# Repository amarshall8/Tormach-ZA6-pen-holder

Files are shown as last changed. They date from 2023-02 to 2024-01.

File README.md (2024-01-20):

# Tormach-ZA6-pen-holder
 A compact, low cost, high precision pen drawing module for Tormach ZA6 robotic arms.\
 More info on the design can be found here https://www.alecmarshall.com/articles/tormach-za6-pen-plotter-module/
 
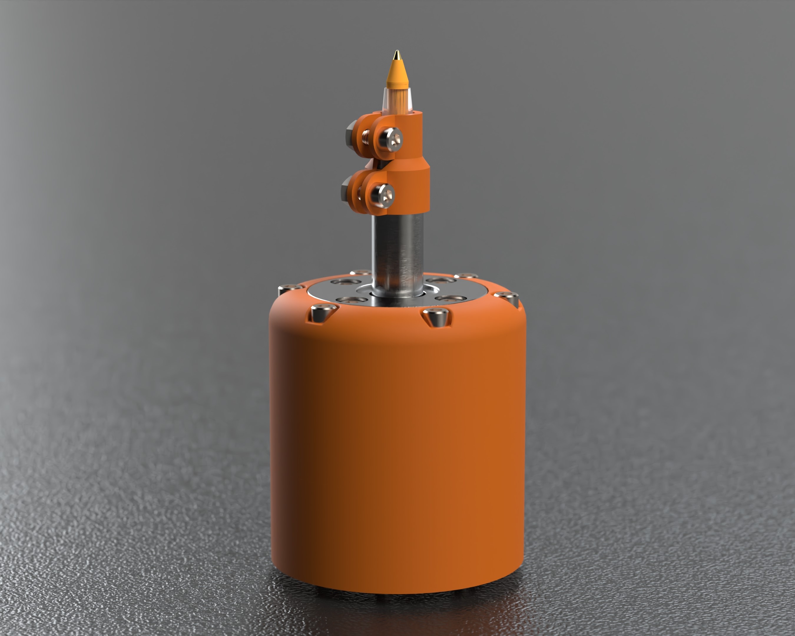
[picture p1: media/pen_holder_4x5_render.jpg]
render


## Required materials:

  * [Compression spring](https://www.mcmaster.com/9657K332/)
  * [12mm steel pipe](https://www.mcmaster.com/6045N11/)
  * [12mm linear bearing with circular flange](https://www.mcmaster.com/6483K114/) (Cheap LM12UU bearing with the same circular flange on eBay are what I used)
  * [1/8" by 1" Steel pin](https://www.mcmaster.com/90145A475/) (for endstop cross bar)
  * __10x__ 6-32 1/4" heat set inserts:
    * [Amazon](https://www.amazon.com/dp/B076R7F3DJ) (select long option)
    * [McMaster](https://www.mcmaster.com/93365A132/)
  * __6x__ 6-32 1-3/4" bolts/screws (To attach the upper section to the lower section)
  * __6x__ M4 25mm bolts/screws (Ideally SHCS. Attaches the lower section to the robotic arm)
  * __4x__ 6-32 1/2" bolts/screws (To attach the linear bearing to the upper section)
  * __2x__ 6-32 3/8" bolts/screws (For compression pen mount)
  * __2x__ 6-32 nuts (For compression pen mount)

## Assembly:

First the 3D printed parts need to have the heatset inserts pushed into the relevant spots on the parts. This should be fairly straightforward.\
There is an [excellent guide](https://hackaday.com/2019/02/28/threading-3d-printed-parts-how-to-use-heat-set-inserts/) for it on Hackaday with recommendations for slicer settings as well.

Next, you may need to sand down a section of the pipe to fit properly. The pipe is not always less than 12mm, and can trend upwards of it, meaning that it will not fit into the linear bearing. To solve this, you can mount the pipe in a drill, and have a second person use 400-600 grit sandpaper to slowly make it thin enough to slide smoothly. Make sure you wipe it with an oiled cloth before running it through the bearing, otherwise this will put metal dust into the bearing, which is not good.
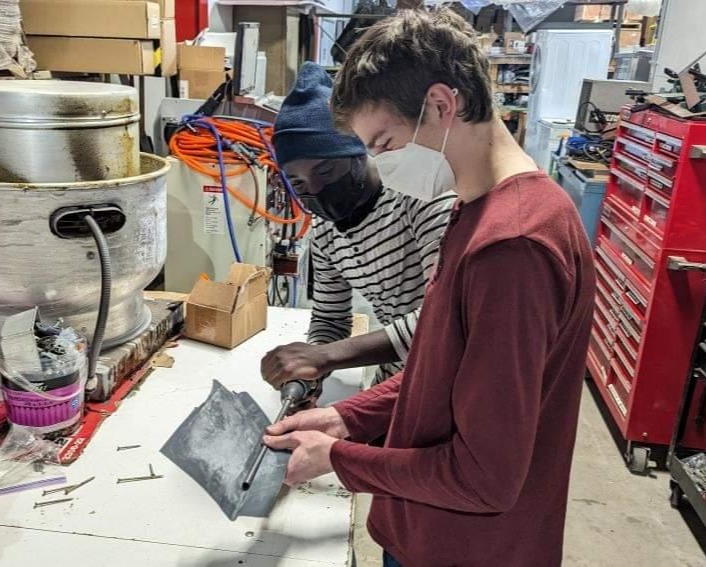
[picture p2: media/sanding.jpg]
sanding


Then, the section of pipe which has the correct diameter will need to be cut to the length specified in the drawing below. I recommend using a bandsaw or hacksaw for this.\
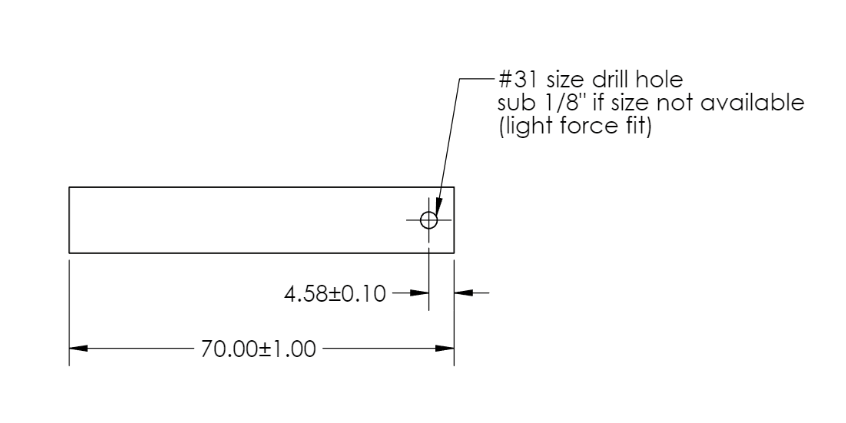
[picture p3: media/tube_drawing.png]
tube


To finish the pipe, a hole needs to be drilled at the distance from the edge specified in the drawing above to fit the 1/8 pin. This can be done by hand, but it is far easier with a drill press or a mill, since the pin can't be skewed much, otherwise it won't fit.
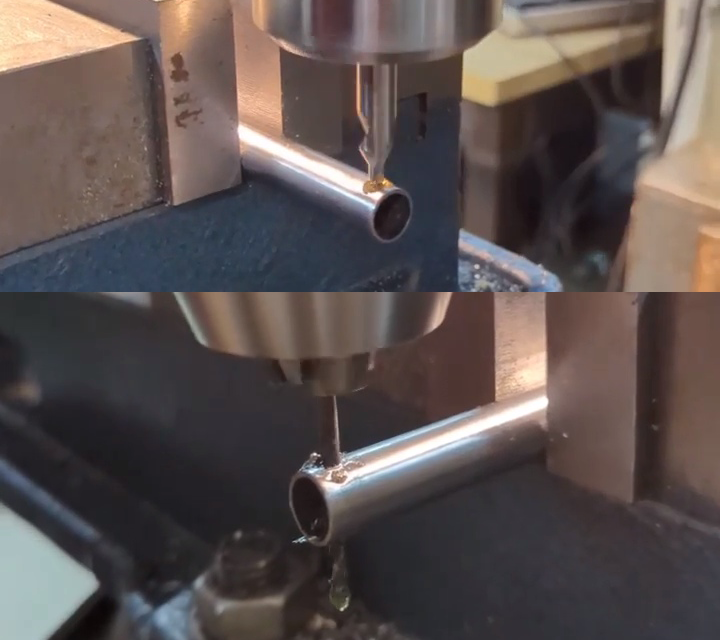
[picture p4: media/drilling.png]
drilling


Finally, the pin can be inserted into the pipe.
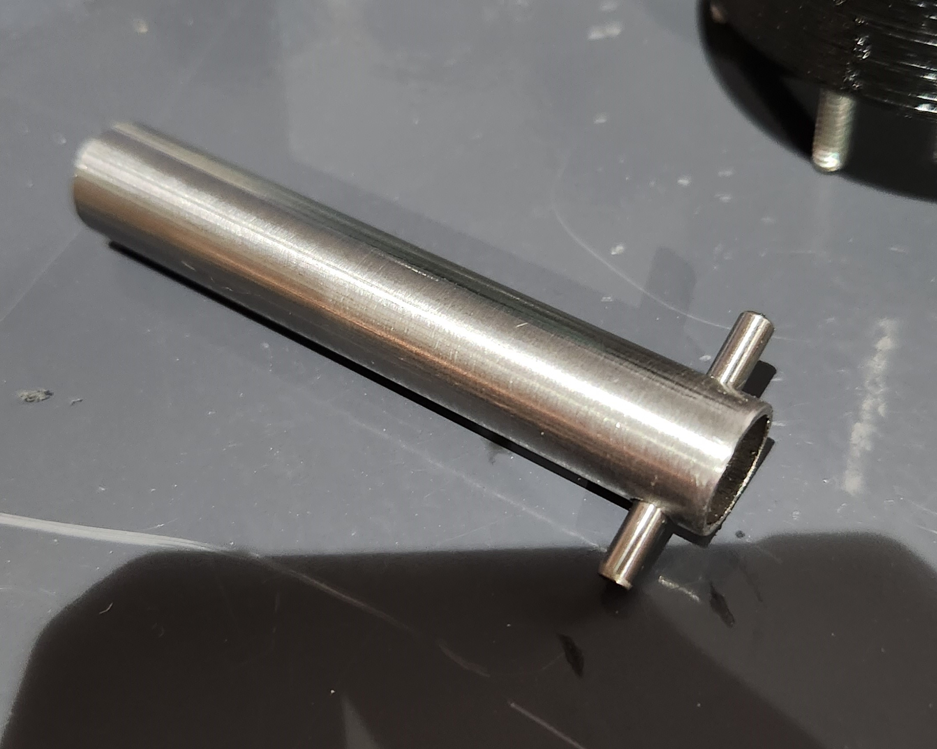
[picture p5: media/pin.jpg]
pin


The last step before assembling it onto the robot is to add the linear bearing to the upper housing 3D print and add the pipe. It should be semi press fit, just push it into the housing and add the four 6-32 1/2in screws to finish the upper housing.
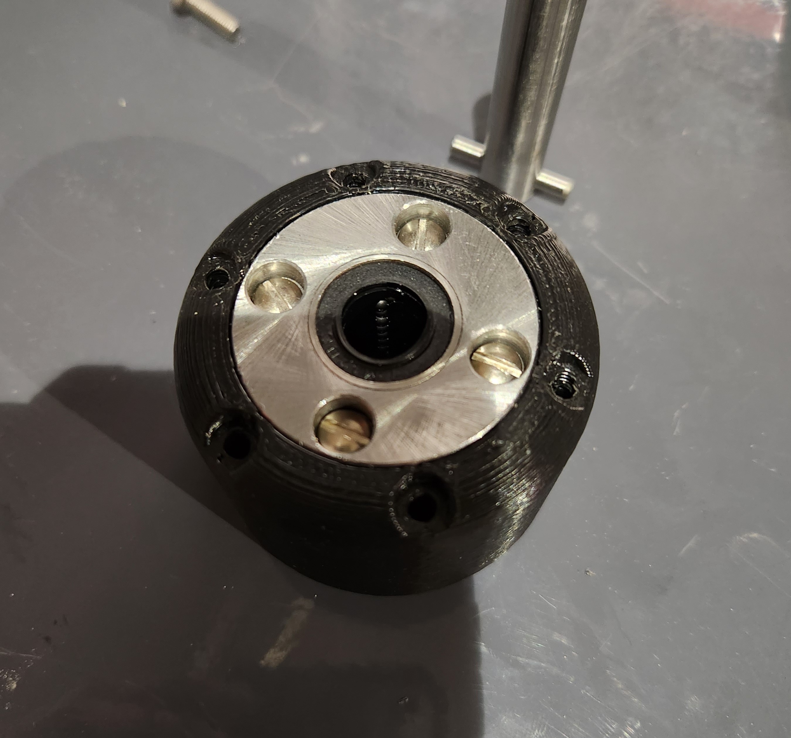
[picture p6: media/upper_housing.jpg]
housing


Next, add the pipe with the cross-pin.
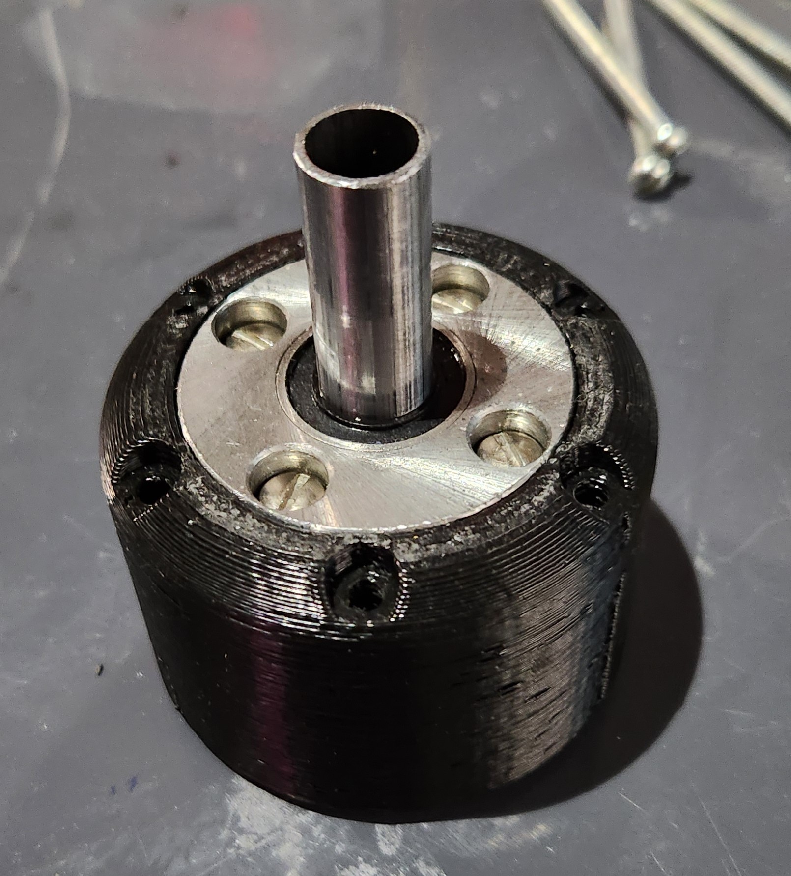
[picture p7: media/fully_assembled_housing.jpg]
housing with pin


### Robot Assembly:

To add the pen holder to the robot, the lower section must be screwed to the robot end-effector before the upper housing can be attached. Through experimentation by Sadiq, we found 3 screws is plenty. Then the spring needs to be inserted into the lower housing, and the plunger seperator piece can be installed.
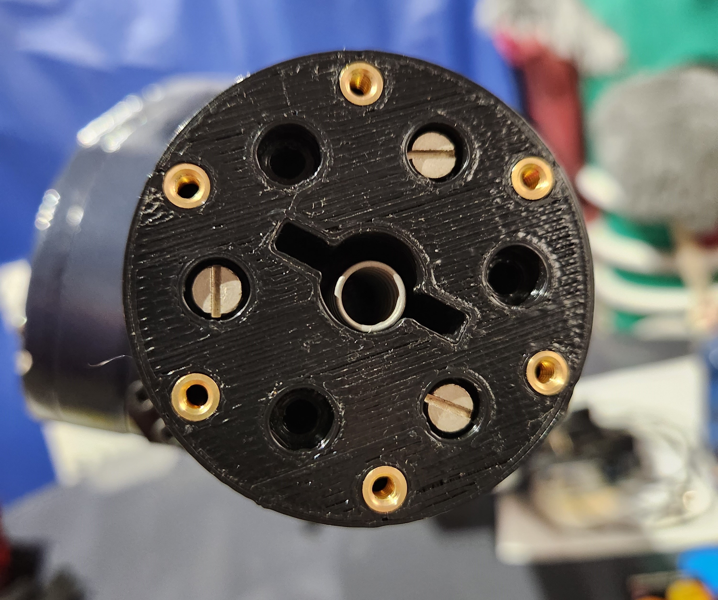
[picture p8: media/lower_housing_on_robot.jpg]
lower housing on robot


Next, use the 6 1-3/4" 6-32 screws to attach the upper housing to the lower housing on the robot. Make sure to compress the spring and keep the plunger seperator in place between the spring and the pipe. Finally, add the pen mount with the two short 6-32 screws and nuts, and tighten them down on the pipe and on the pen. Too much force will break the print!.
Note: you may have to cut down your pen to fit inside the pipe without it sticking out a ton!
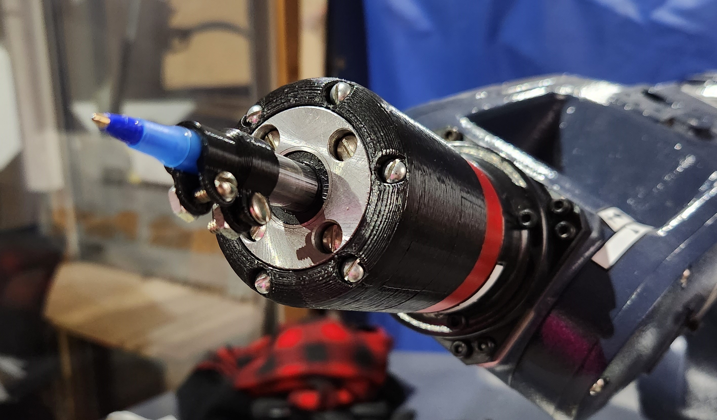
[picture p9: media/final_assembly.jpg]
final assembly


Congratulations, you now have a Tormach ZA6 robot capable of precise drawing!! :)

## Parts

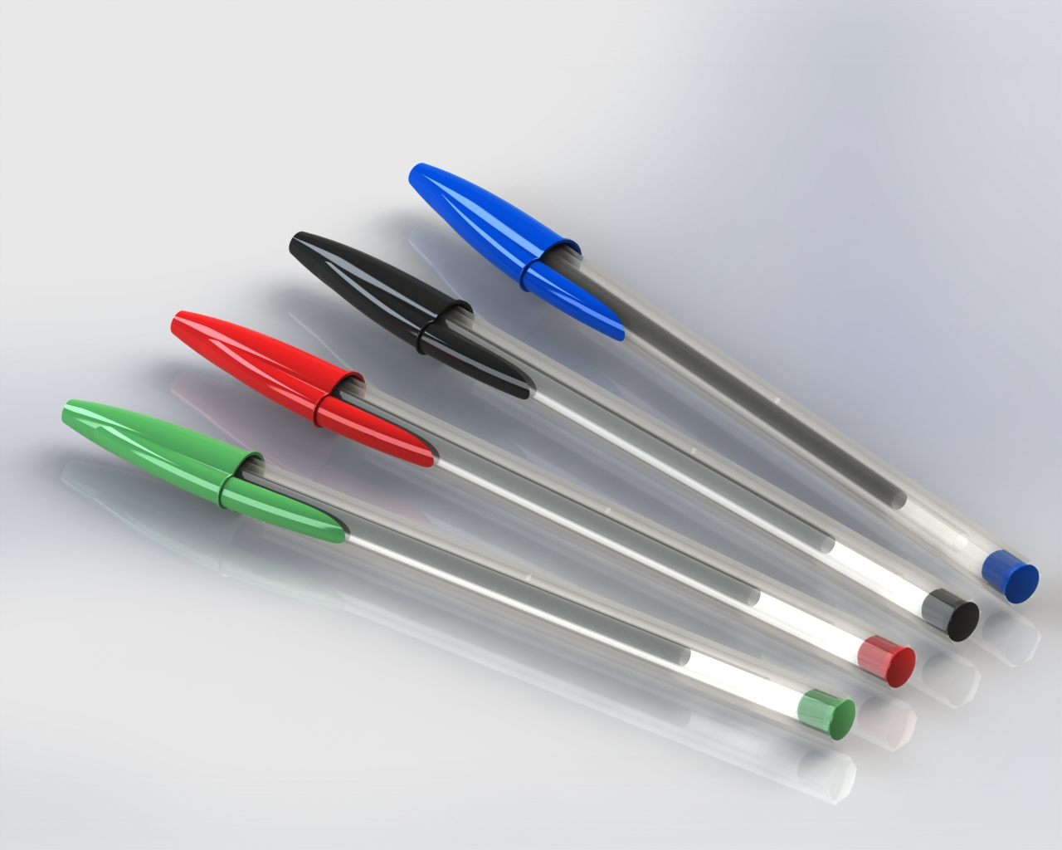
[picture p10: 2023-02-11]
mcmaster parts/bic-ballpoint-pen-boligrafo-bic-1.snapshot.3/conjunto.JPG

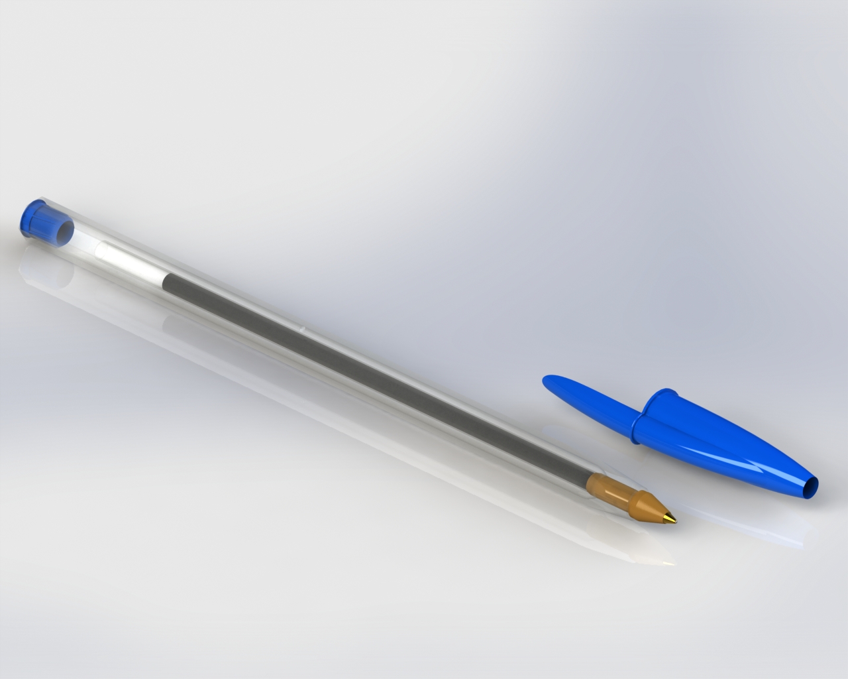
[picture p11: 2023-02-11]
mcmaster parts/bic-ballpoint-pen-boligrafo-bic-1.snapshot.3/boligrafo.JPG

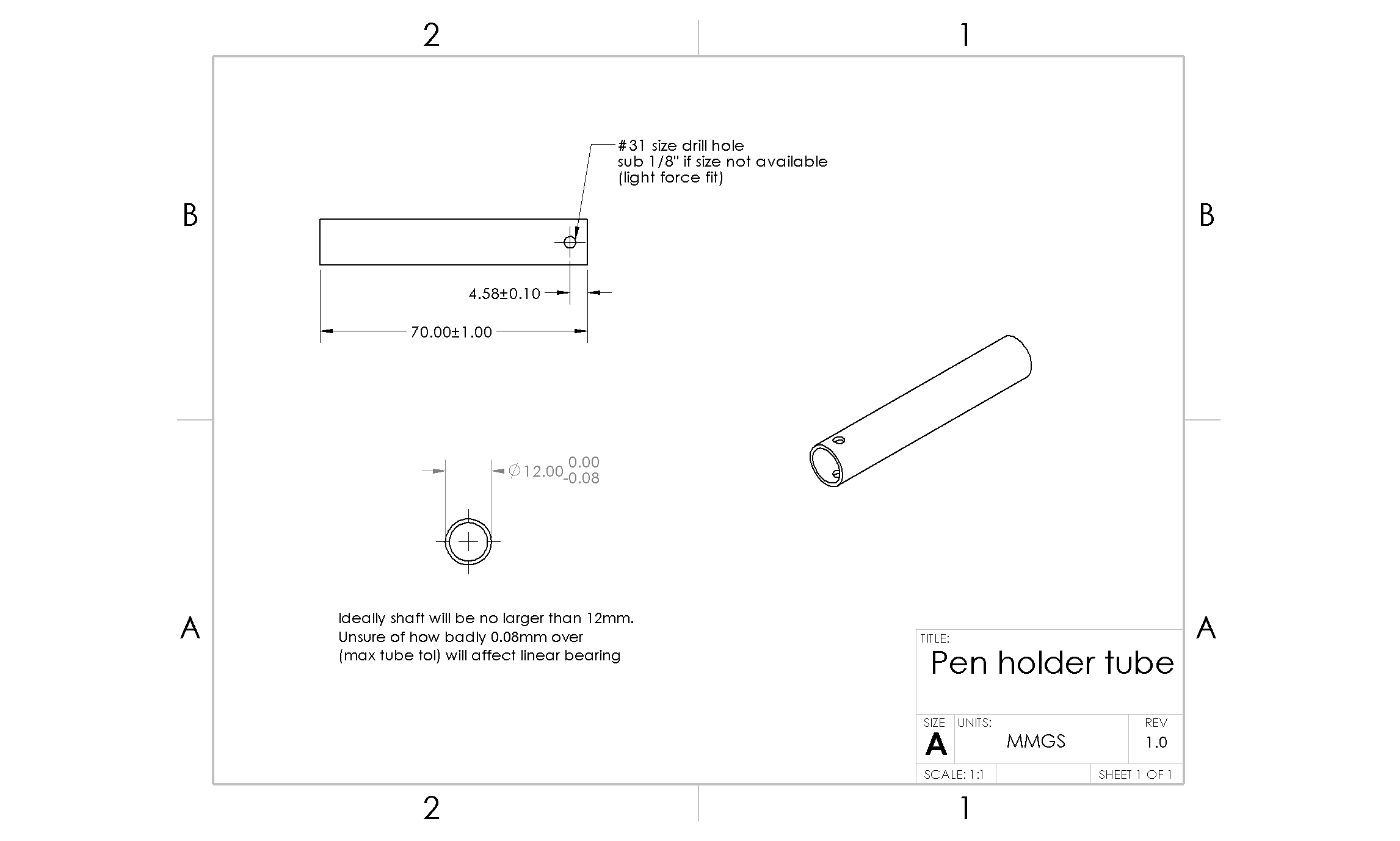
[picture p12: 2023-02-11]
mcmaster parts/6045N111_Low-Carbon Steel Round Tube.PNG

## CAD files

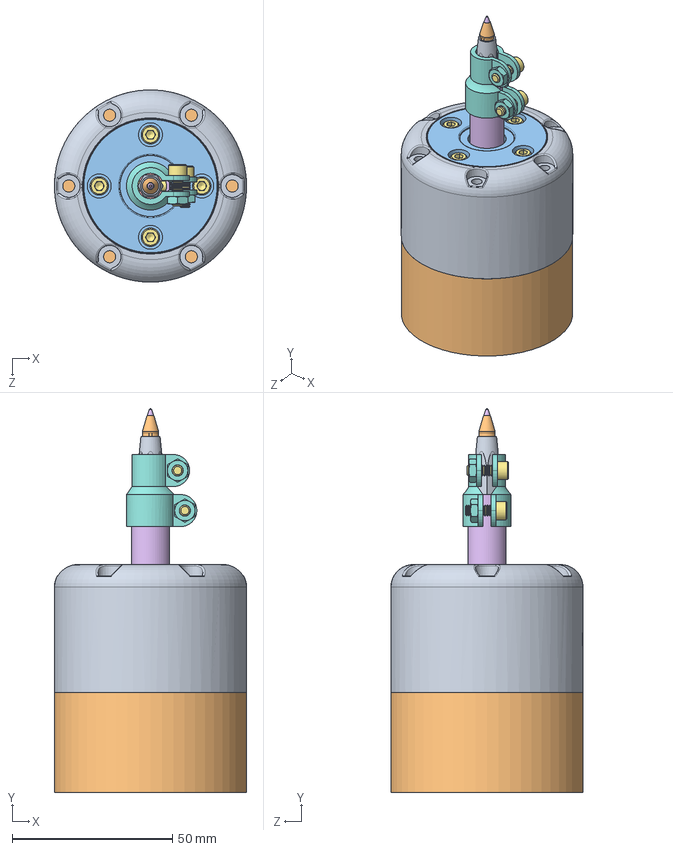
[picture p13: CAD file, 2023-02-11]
Pen assembly.SLDASM
60.0 x 119.9 x 60.0 mm
Lower Section
6483K114_Flange-Mounted Linear Ball Bearing
Upper Section
1986K94_302 Stainless Steel Corrosion-Resistant Compression Springs
Plunger
6045N111_Low-Carbon Steel Round Tube
Pin
Pen adapter
tubo
cabeza
tubo_tinta
tinta
bola
cabezal
socket head cap screw_ai x 6
90730A007_18-8 Stainless Steel Narrow Hex Nut x 2

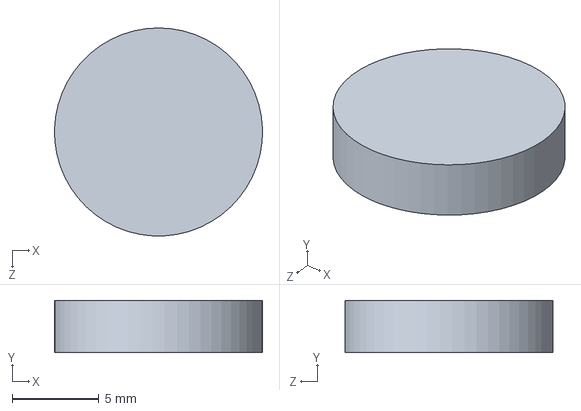
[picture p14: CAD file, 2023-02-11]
Plunger.SLDPRT
12.0 x 3.00 x 12.0 mm

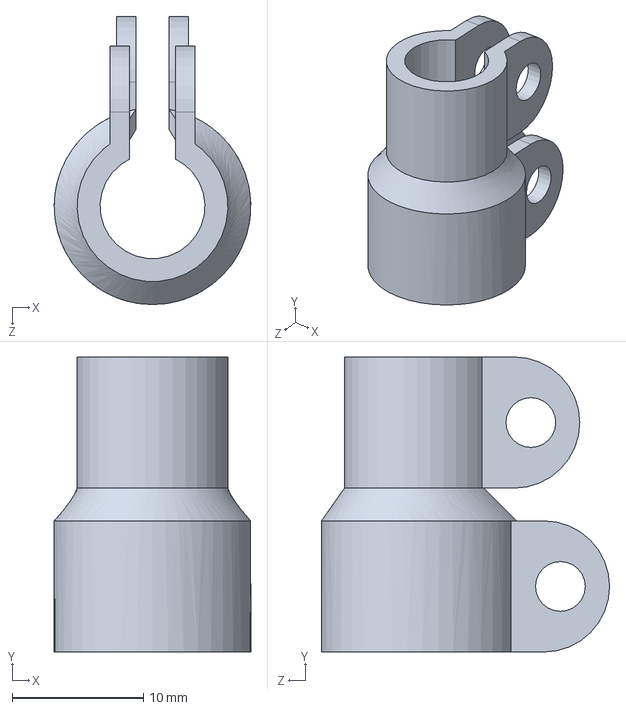
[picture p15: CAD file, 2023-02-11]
Pen adapter.SLDPRT
15.0 x 22.5 x 22.0 mm

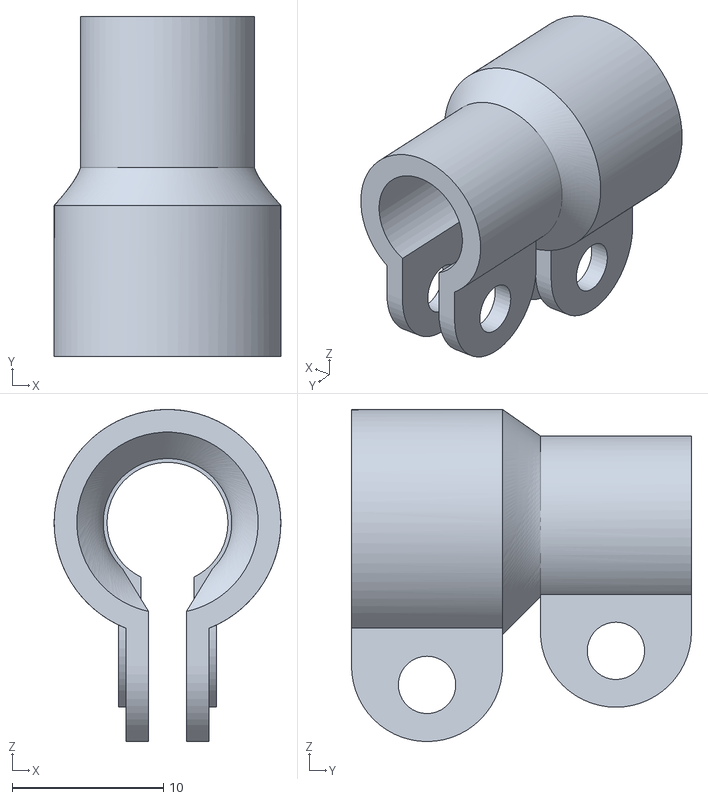
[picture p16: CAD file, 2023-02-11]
STLs for 3D printing/Pen adapter.STL
15.0 x 22.5 x 22.0

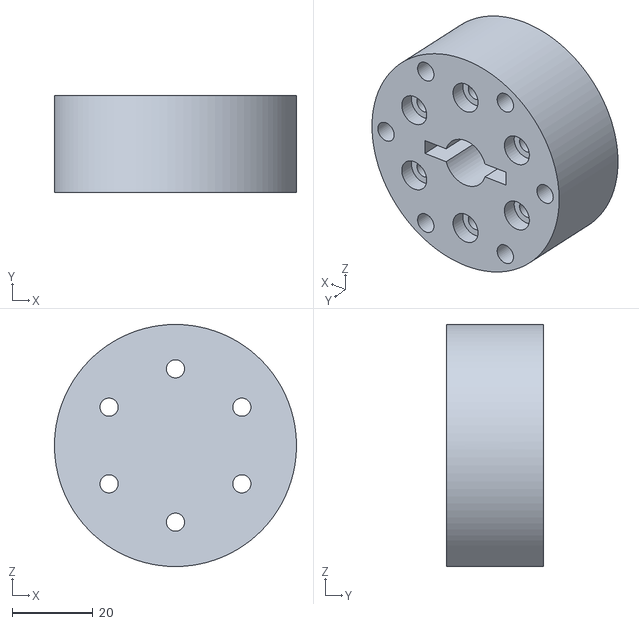
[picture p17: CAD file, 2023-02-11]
STLs for 3D printing/Lower Section.STL
60.0 x 24.2 x 60.0

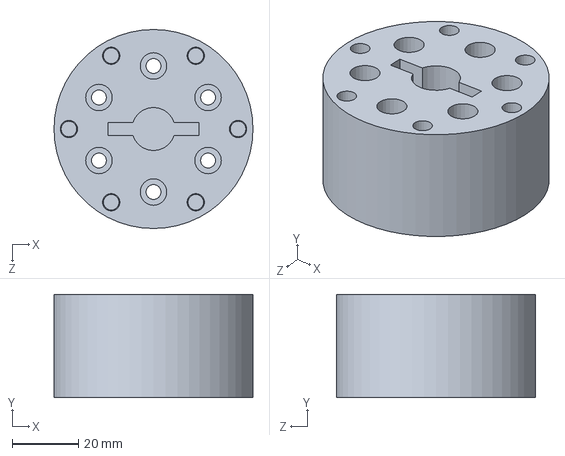
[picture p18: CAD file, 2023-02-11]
Lower Section.SLDPRT
60.0 x 31.2 x 60.0 mm

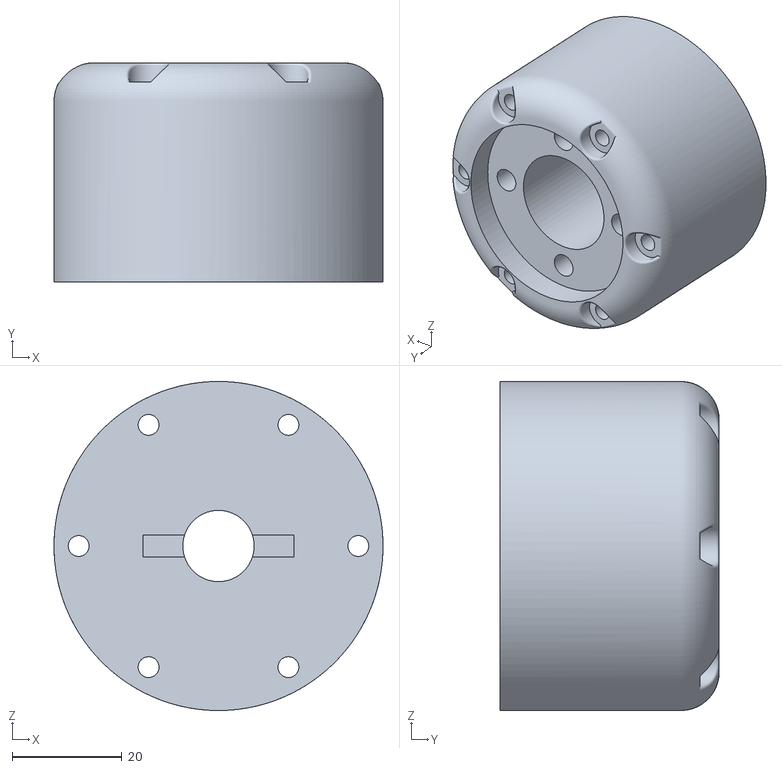
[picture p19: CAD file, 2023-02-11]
STLs for 3D printing/Upper Section (2.0).STL
60.0 x 40.0 x 60.0

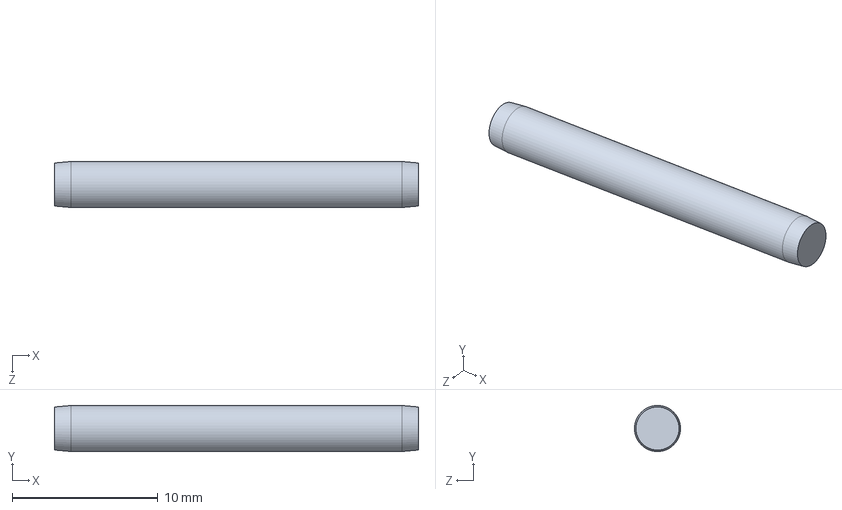
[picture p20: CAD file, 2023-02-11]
Pin.SLDPRT
25.0 x 3.16 x 3.16 mm

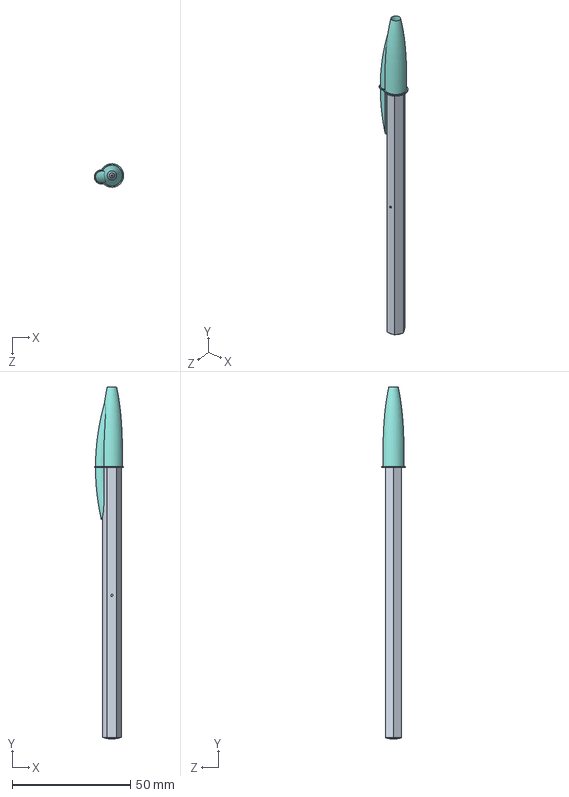
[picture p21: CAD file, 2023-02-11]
mcmaster parts/bic-ballpoint-pen-boligrafo-bic-1.snapshot.3/Ensamblaje.SLDASM
12.4 x 148.7 x 9.99 mm
tubo
tapon
cabeza
tubo_tinta
tinta
bola
cabezal
capucha

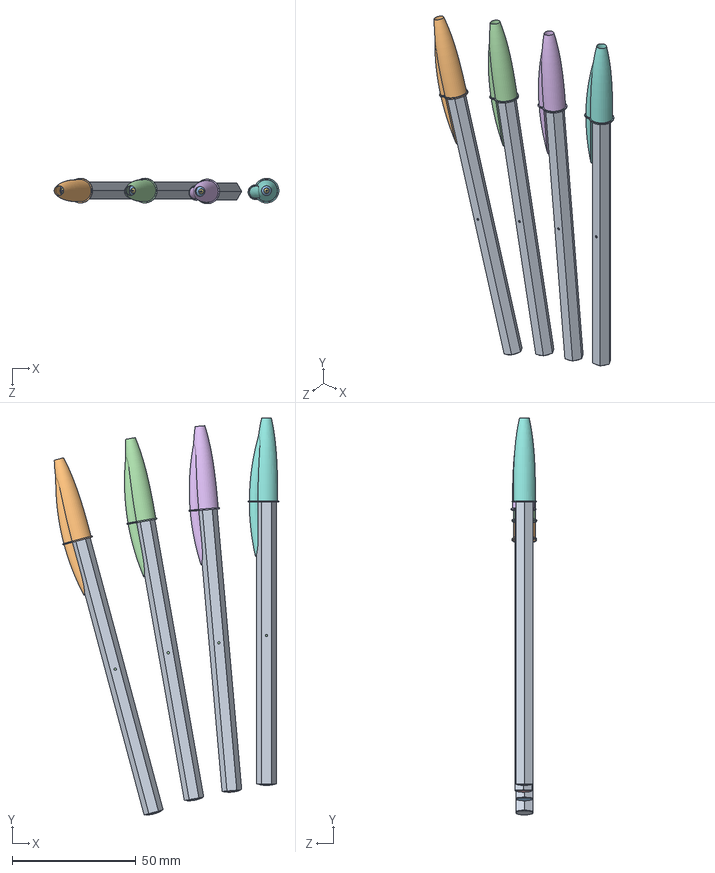
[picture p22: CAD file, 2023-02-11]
mcmaster parts/bic-ballpoint-pen-boligrafo-bic-1.snapshot.3/Conjunto.SLDASM
90.9 x 160.6 x 10.3 mm
tubo x 4
tapon
cabeza x 4
tubo_tinta x 4
tinta x 4
bola x 4
cabezal x 4
capucha
tapon_v
capucha_v
tapon_r
capucha_r
tapon_n
capucha_n

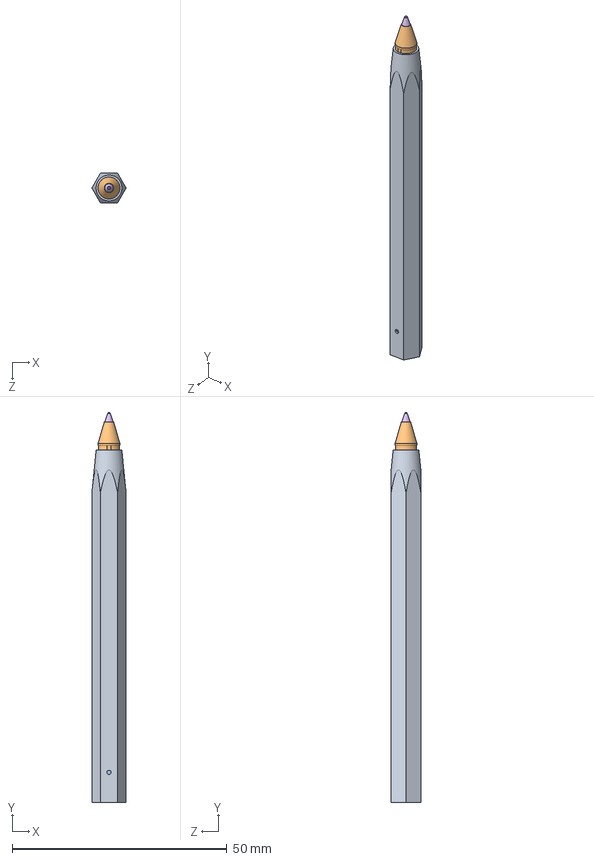
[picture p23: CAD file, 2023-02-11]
mcmaster parts/bic-ballpoint-pen-boligrafo-bic-1.snapshot.3/ens_azul2.SLDASM
8.00 x 90.7 x 6.93 mm
tubo
cabeza
tubo_tinta
tinta
bola
cabezal

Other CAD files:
STLs for 3D printing/Plunger seperator.STL
STLs for 3D printing/Upper Section.STL
STLs for 3D printing/Lower Section (2.0).STL
Upper Section.SLDPRT
mcmaster parts/bic-ballpoint-pen-boligrafo-bic-1.snapshot.3/ensa_verde.SLDASM
mcmaster parts/bic-ballpoint-pen-boligrafo-bic-1.snapshot.3/ens_azul.SLDASM
mcmaster parts/bic-ballpoint-pen-boligrafo-bic-1.snapshot.3/ensa_negro.SLDASM
mcmaster parts/6045N111_Low-Carbon Steel Round Tube.SLDDRW
mcmaster parts/6045N111_Low-Carbon Steel Round Tube.SLDPRT
mcmaster parts/6483K114_Flange-Mounted Linear Ball Bearing.SLDPRT
mcmaster parts/90730A007_18-8 Stainless Steel Narrow Hex Nut.SLDPRT
mcmaster parts/9657K332_Compression Spring.SLDPRT
mcmaster parts/bic-ballpoint-pen-boligrafo-bic-1.snapshot.3/Ens_negro/capucha_n.SLDPRT
mcmaster parts/bic-ballpoint-pen-boligrafo-bic-1.snapshot.3/Ens_negro/tapon_n.SLDPRT
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

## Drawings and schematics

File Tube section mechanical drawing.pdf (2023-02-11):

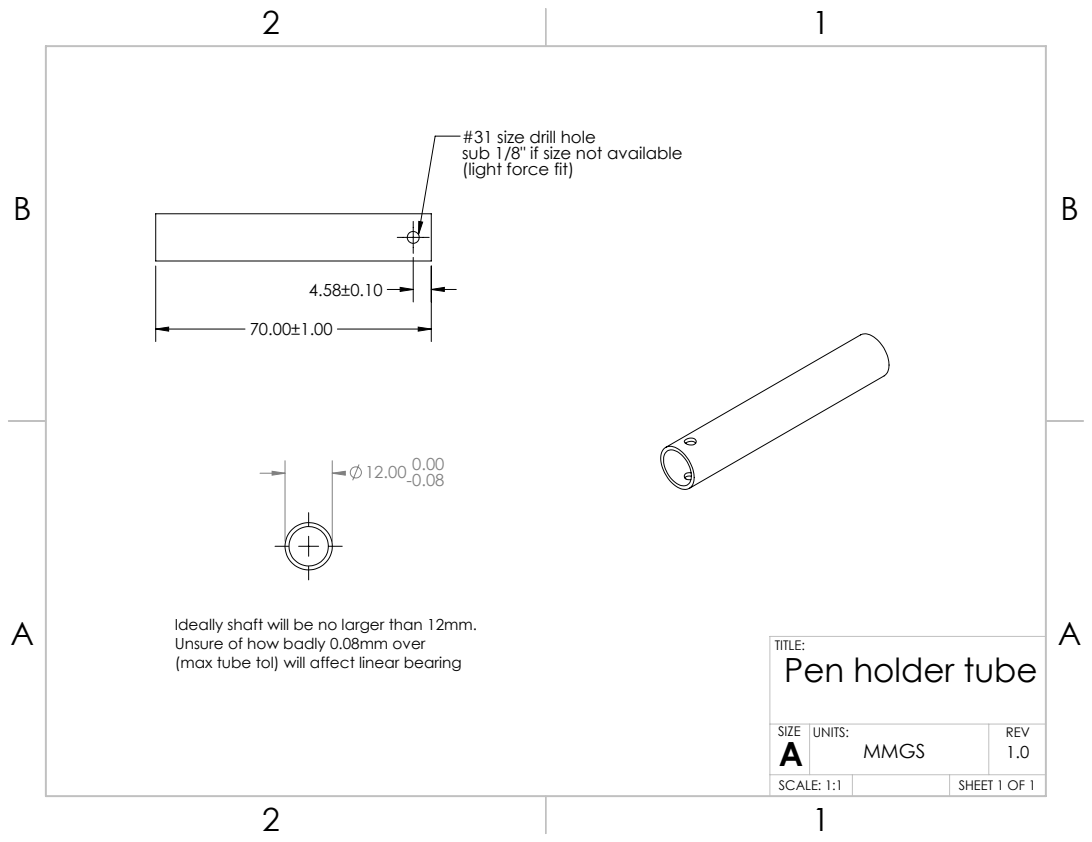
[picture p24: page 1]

#31 size drill hole
sub 1/8" if size not available
(light force fit)

Ideally shaft will be no larger than 12mm.
Unsure of how badly 0.08mm over
(max tube tol) will affect linear bearing

Pen holder tube

SIZE A | UNITS: MMGS | REV 1.0

SCALE: 1:1 | | SHEET 1 OF 1

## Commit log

2023-02-11 Moving files to github for public access
    [1986K94_302 Stainless Steel Corrosion-Resistant Compression Springs.SLDPRT, 6045N111_Low-Carbon Steel Round Tube.SLDDRW, 6045N111_Low-Carbon Steel Round Tube.S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]
2023-02-11 Rearranging files and updating assembly
    Added a .STEP version of the assembly as well for non-SOLIDWORKS users
    [Plunger seperator.STL, Plunger.SLDDRW, Plunger.SLDPRT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]
2023-02-11 Changed assembly and updated parts
    [1986K94_302 Stainless Steel Corrosion-Resistant Compression Springs.SLDPRT, 90730A007_18-8 Stainless Steel Narrow Hex Nut.SLDPRT, 9657K332_Compression Spring.S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]
